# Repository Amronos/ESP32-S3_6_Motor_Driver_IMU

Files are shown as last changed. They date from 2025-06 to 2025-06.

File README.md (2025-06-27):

# ESP32-S3 6 Motor Driver with IMU

**_This board is currently in development._**

This board features an **ESP32-S3** microcontroller, a **6-channel** DC **motor driver**, and an integrated **BNO086 IMU** for precise motion and orientation data.<br>
It supports **encoder feedback**, enabling accurate position control. Motors can be driven at voltages up to **36V**.

This board is perfect for robots requiring more than two motors.<br>
Simply wire your motors, connect the board to a PC, another microcontroller, or even your phone/tablet and use the ESP32-S3's versatile communication options like I2C, SPI, UART, Wi-Fi, and Bluetooth to control your robot.

A full **Arduino library** for the board is available that allows you to control the motors, IMU, and read data from the encoders.<br>
Sample **ROS 2** packages are also available, that show the recommended usage of the board with ROS 2.

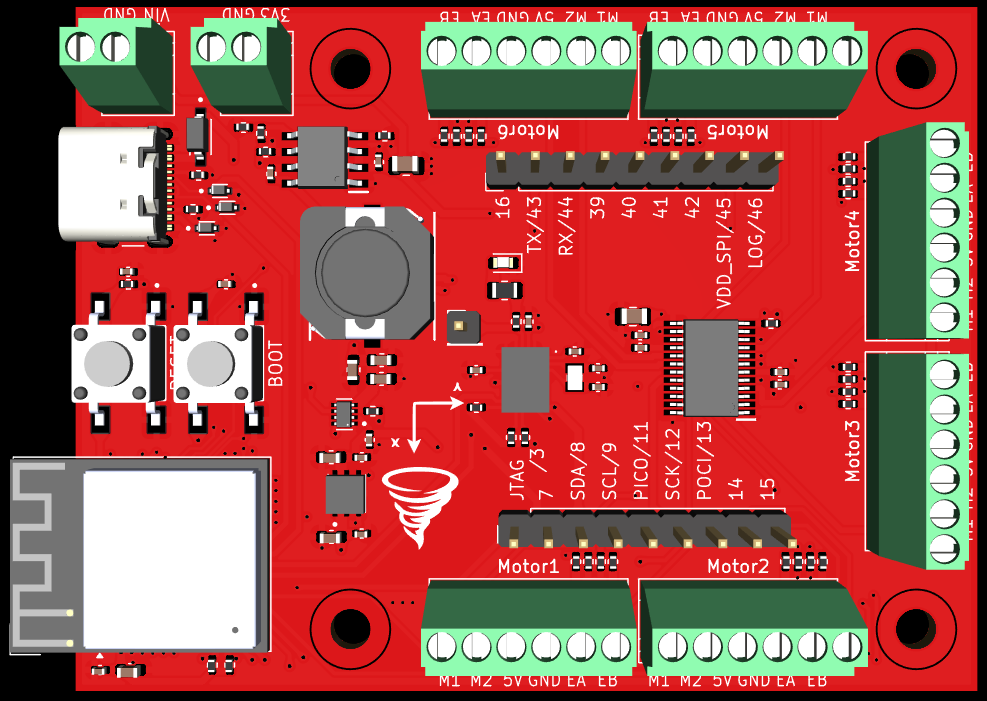
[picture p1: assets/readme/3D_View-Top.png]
3D Model - Top


## 📂 About this Repository

This repository contains all code, design files, and information related to the ESP32-S3 6 Motor Driver with IMU.

### Directory Information

- [assets/](assets/): Assets used throughout this repository.
- [hardware_design/](hardware_design/): Complete KiCad project design files, schematic, 3D model, and BOM.

### Related Repositories

- [ESP32-S3_6_Motor_Driver_IMU_Library](https://github.com/amronos/ESP32-S3_6_Motor_Driver_IMU_Library/): Arduino library for the board.

## 📷 Images

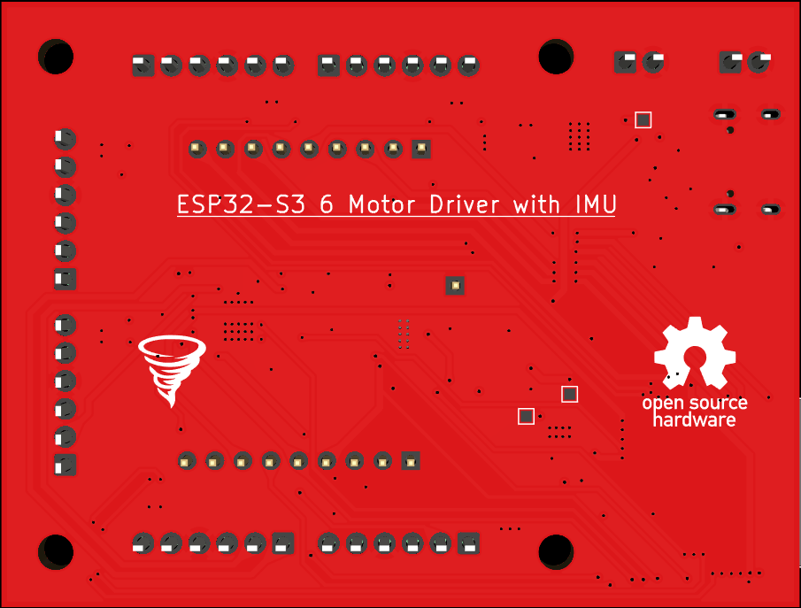
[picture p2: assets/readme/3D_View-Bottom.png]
3D Model - Bottom

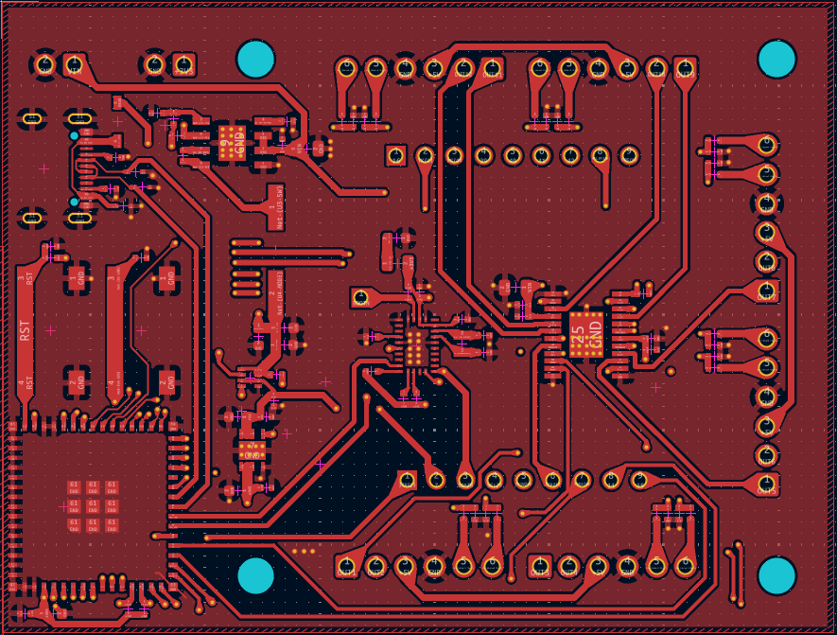
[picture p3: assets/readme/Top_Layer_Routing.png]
Top Layer Routing


## Costs

| Item | Price (USD) |
| --- | --- |
| Full PCB Manufacturing | $ 113.79 |
| Shipping | $ 25 |
| **Subtotal** | $ 138.79 |

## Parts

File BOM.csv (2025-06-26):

Designator | Footprint | Value | Manufacturer | Mfr. Part No. | Quantity
C1, C16 | 0805 | 10 µF | Murata Electronics | GRM21BR61H106KE43L | 2
C10, C11, C13, C15, C17, C18, C2, C21, C23, C24, C25, C3, C8, C9 | 0402 | 100 nF | Samsung Electro-Mechanics | CL05B104KB54PNC | 14
C12, C14, C7 | 0603 | 10 µF | Murata Electronics | GRT188R61E106ME13D | 3
C19 | 0402 | 4.7 µF | Murata Electronics | GRT155R61A475ME13D | 1
C20, C22 | 0402 | 22 pF | Murata Electronics | GCM1555C1H220FA16D | 2
C4, C5, C6 | 0603 | 22 µF | Murata Electronics | GRT188R61A226ME13D | 3
D1 | SOD3715X145N | 1N5819HW-7-F | Diodes Incorporated | 1N5819HW-7-F | 1
D2, D3, D4 | TVS_LESD5D5.0CT1G | LESD5D5.0CT1G | LRC | LESD5D5.0CT1G | 3
D5 | 0603 | LED | ROHM Semiconductor | SML-D12V8WT86C | 1
J1 | USB_C_Receptacle_GCT_USB4105-xx-A_16P_TopMnt_Horizontal | USB_C_Receptacle_USB2.0_16P | GCT | USB4105-GF-A | 1
J2, J3 | PinHeader_1x09_P2.54mm_Vertical | Conn_01x09 | Generic | Generic | 2
J4 | PinHeader_1x01_P2.54mm_Vertical | Conn_01x01 | Generic | Generic | 1
J5, J6 | TerminalBlock_Xinya_XY308-2.54-2P_1x02_P2.54mm_Horizontal | Screw_Terminal_01x02 | XINYA | XY308-2.54-2P | 2
L1 | INDPM102100X400N | 15 µH | Coilcraft | MSS1038-153MLC | 1
MOTOR1, MOTOR2, MOTOR3, MOTOR4, MOTOR5, MOTOR6 | TerminalBlock_Xinya_XY308-2.54-6P_1x06_P2.54mm_Horizontal | Screw_Terminal_01x06 | XINYA | XY308-2.54-6P | 6
R1, R2 | 0402 | 5.1 kΩ | Panasonic Electronic Components | ERA-2AED512X | 2
R10, R15, R16, R20, R22, R24, R26, R28, R3, R30, R32, R34, R36, R38, R39, R4, R5, R9 | 0402 | 10 kΩ | Panasonic Electronic Components | ERA-2AEB103X | 18
R11, R12, R17, R18 | 0402 | 4.7 kΩ | Panasonic Electronic Components | ERA-2AEB472X | 4
R13, R14, R19, R21, R23, R25, R27, R29, R31, R33, R35, R37 | 0402 | 20 kΩ | Panasonic Electronic Components | ERA-2AEB203X | 12
R40 | 0603 | 51 Ω | Panasonic Electronic Components | ERA-3AEB510V | 1
R6 | 0402 | 64.9 kΩ | Panasonic Electronic Components | ERA-2AEB6492X | 1
R7 | 0402 | 100 kΩ | Panasonic Electronic Components | ERA-2AEB104X | 1
R8 | 0402 | 24.9 kΩ | Panasonic Electronic Components | ERA-2AEB2492X | 1
SW1, SW2 | SW_3-1437565-0 | 3-1437565-0 | TE Connectivity | 3-1437565-0 | 2
U1 | ESP32-S2-MINI-1 | ESP32-S3-MINI-1 | Espressif Systems | ESP32-S3-MINI-1-N8 | 1
U2 | SON95P300X300X100-7N | LD39200PU33R | STMicroelectronics | LD39200PU33R | 1
U3 | SOIC127P600X170-9N | LMR38020FDDAR | Texas Instruments | LMR38020FDDAR | 1
U4 | SOTFL50P160X60-8N | TPS2116DRLR | Texas Instruments | TPS2116DRLR | 1
U5 | SOP65P640X120-25N | DRV8912QPWPRQ1 | Texas Instruments | DRV8912QPWPRQ1 | 1
U6 | BNO086 | BNO086 | Ceva | BNO086 | 1
Y1 | CM8V32768TA020125 | 32.768 kHz | Micro Crystal | CM8V-T1A-32.768kHz-12.5pF-20PPM-TB-QA | 1

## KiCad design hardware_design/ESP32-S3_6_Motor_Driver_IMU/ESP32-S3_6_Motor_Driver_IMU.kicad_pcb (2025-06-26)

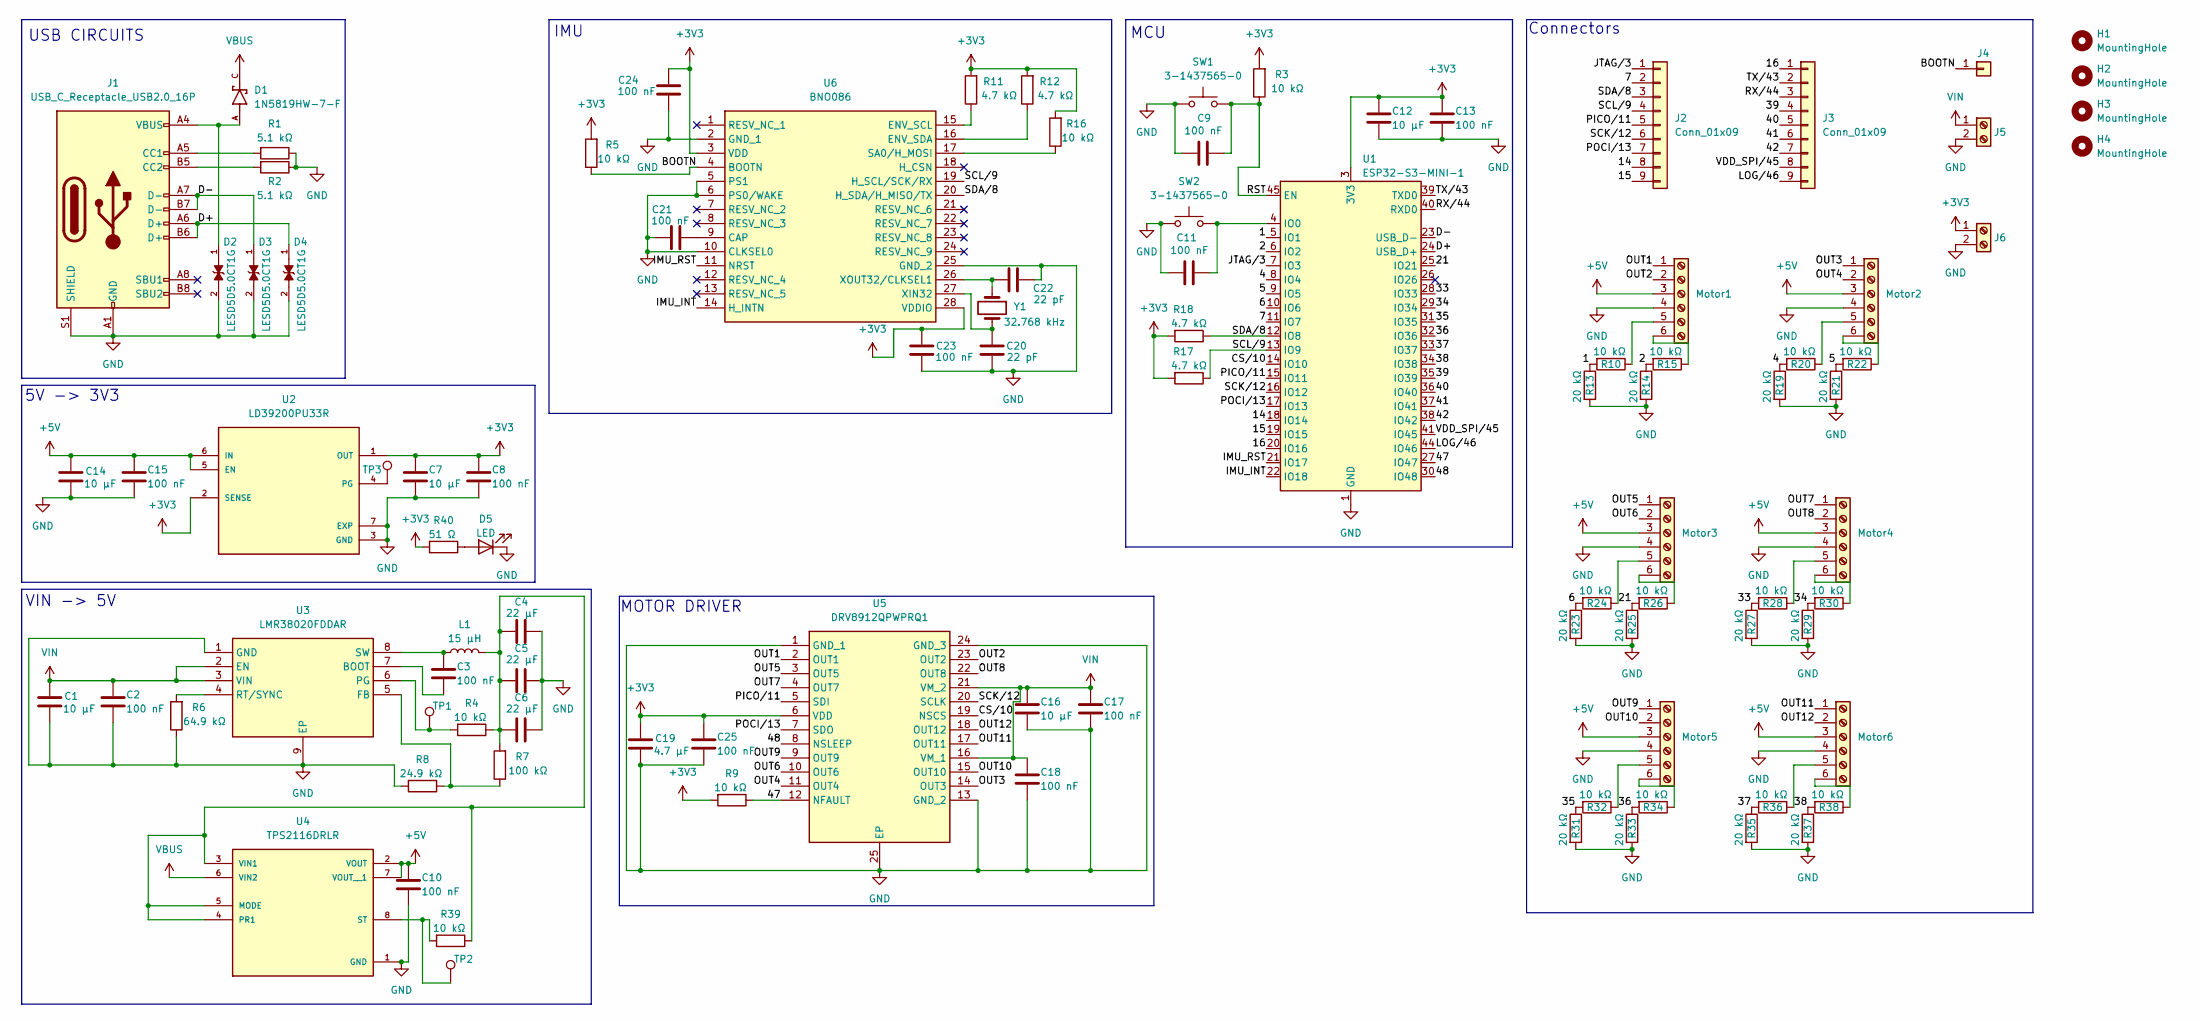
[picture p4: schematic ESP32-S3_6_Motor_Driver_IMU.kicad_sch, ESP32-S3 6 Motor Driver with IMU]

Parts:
C1, C16: 10 µF; C_0805_2012Metric
C2, C3, C8, C9, C10, C11, C13, C15, C17, C18, C21, C23, C24, C25: 100 nF; C_0402_1005Metric
C4, C5, C6: 22 µF; C_0603_1608Metric
C7, C12, C14: 10 µF; C_0603_1608Metric
C19: 4.7 µF; C_0402_1005Metric
C20, C22: 22 pF; C_0402_1005Metric
D1: 1N5819HW-7-F; SOD3715X145N
D2, D3, D4: LESD5D5.0CT1G; TVS_LESD5D5.0CT1G
D5: LED; LED_0603_1608Metric
H1, H2, H3, H4: MountingHole; MountingHole_3.2mm_M3
J1: USB_C_Receptacle_USB2.0_16P; USB_C_Receptacle_GCT_USB4105-xx-A_16P_TopMnt_Horizontal
J2, J3: Conn_01x09; PinHeader_1x09_P2.54mm_Vertical
J4: Conn_01x01; PinHeader_1x01_P2.54mm_Vertical
J5, J6: Screw_Terminal_01x02; TerminalBlock_Xinya_XY308-2.54-2P_1x02_P2.54mm_Horizontal
L1: 15 µH; INDPM102100X400N
Motor1, Motor2, Motor3, Motor4, Motor5, Motor6: Screw_Terminal_01x06; TerminalBlock_Xinya_XY308-2.54-6P_1x06_P2.54mm_Horizontal
R1, R2: 5.1 kΩ; R_0402_1005Metric
R3, R4, R5, R9, R10, R15, R16, R20, R22, R24, R26, R28, R30, R32, R34, R36, R38, R39: 10 kΩ; R_0402_1005Metric
R6: 64.9 kΩ; R_0402_1005Metric
R7: 100 kΩ; R_0402_1005Metric
R8: 24.9 kΩ; R_0402_1005Metric
R11, R12, R17, R18: 4.7 kΩ; R_0402_1005Metric
R13, R14, R19, R21, R23, R25, R27, R29, R31, R33, R35, R37: 20 kΩ; R_0402_1005Metric
R40: 51 Ω; R_0805_2012Metric
SW1, SW2: 3-1437565-0; SW_3-1437565-0
TP1, TP2, TP3: TestPoint; TestPoint_Pad_1.0x1.0mm
U1: ESP32-S3-MINI-1; ESP32-S2-MINI-1
U2: LD39200PU33R; SON95P300X300X100-7N
U3: LMR38020FDDAR; SOIC127P600X170-9N
U4: TPS2116DRLR; SOTFL50P160X60-8N
U5: DRV8912QPWPRQ1; SOP65P640X120-25N
U6: BNO086
Y1: 32.768 kHz; CM8V32768TA020125

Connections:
+3V3: C7.1, C8.1, C12.1, C13.1, C19.1, C23.1, C24.2, C25.1, J6.1, R3.2, R5.2, R9.2, R11.2, R12.2, R16.2, R17.2, R18.2, R40.2, U1.3 (3V3), U2.1 (OUT), U2.2 (SENSE), U5.6 (VDD), U6.3 (VDD), U6.28 (VDDIO)
+5V: C10.1, C14.1, C15.1, Motor1.3, Motor2.3, Motor3.3, Motor4.3, Motor5.3, Motor6.3, U2.5 (EN), U2.6 (IN), U4.2 (VOUT), U4.7 (VOUT__1)
/1: R10.2, R13.1, U1.5 (IO1)
/2: R14.1, R15.2, U1.6 (IO2)
/4: R19.1, R20.2, U1.8 (IO4)
/5: R21.1, R22.2, U1.9 (IO5)
/6: R23.1, R24.2, U1.10 (IO6)
/7: J2.2, U1.11 (IO7)
/14: J2.8, U1.18 (IO14)
/15: J2.9, U1.19 (IO15)
/16: J3.1, U1.20 (IO16)
/21: R25.1, R26.2, U1.25 (IO21)
/33: R27.1, R28.2, U1.28 (IO33)
/34: R29.1, R30.2, U1.29 (IO34)
/35: R31.1, R32.2, U1.31 (IO35)
/36: R33.1, R34.2, U1.32 (IO36)
/37: R35.1, R36.2, U1.33 (IO37)
/38: R37.1, R38.2, U1.34 (IO38)
/39: J3.4, U1.35 (IO39)
/40: J3.5, U1.36 (IO40)
/41: J3.6, U1.37 (IO41)
/42: J3.7, U1.38 (IO42)
/47: R9.1, U1.27 (IO47), U5.12 (NFAULT)
/48: U1.30 (IO48), U5.8 (NSLEEP)
/BOOTN: J4.1, R5.1, U6.4 (BOOTN)
/CS/10: U1.14 (IO10), U5.19 (NSCS)
/D+: D4.1, J1.A6 (D+), J1.B6 (D+), U1.24 (USB_D+)
/D-: D3.1, J1.A7 (D-), J1.B7 (D-), U1.23 (USB_D-)
/IMU_INT: U1.22 (IO18), U6.14 (H_INTN)
/IMU_RST: U1.21 (IO17), U6.11 (NRST)
/JTAG/3: J2.1, U1.7 (IO3)
/LOG/46: J3.9, U1.44 (IO46)
/OUT1: Motor1.1, U5.2 (OUT1)
/OUT2: Motor1.2, U5.23 (OUT2)
/OUT3: Motor2.1, U5.14 (OUT3)
/OUT4: Motor2.2, U5.11 (OUT4)
/OUT5: Motor3.1, U5.3 (OUT5)
/OUT6: Motor3.2, U5.10 (OUT6)
/OUT7: Motor4.1, U5.4 (OUT7)
/OUT8: Motor4.2, U5.22 (OUT8)
/OUT9: Motor5.1, U5.9 (OUT9)
/OUT10: Motor5.2, U5.15 (OUT10)
/OUT11: Motor6.1, U5.17 (OUT11)
/OUT12: Motor6.2, U5.18 (OUT12)
/PICO/11: J2.5, U1.15 (IO11), U5.5 (SDI)
/POCI/13: J2.7, U1.17 (IO13), U5.7 (SDO)
/RST: C9.2, R3.1, SW1.3 (B), SW1.4 (B), U1.45 (EN)
/RX/44: J3.3, U1.40 (RXD0)
/SCK/12: J2.6, U1.16 (IO12), U5.20 (SCLK)
/SCL/9: J2.4, R17.1, U1.13 (IO9), U6.19 (H_SCL/SCK/RX)
/SDA/8: J2.3, R18.1, U1.12 (IO8), U6.20 (H_SDA/H_MISO/TX)
/TX/43: J3.2, U1.39 (TXD0)
/VDD_SPI/45: J3.8, U1.41 (IO45)
GND: C1.2, C2.2, C4.2, C5.2, C6.2, C7.2, C8.2, C9.1, C10.2, C11.1, C12.2, C13.2, C14.2, C15.2, C16.2, C17.2, C18.2, C19.2, C20.2, C21.1, C22.2, C23.2, C24.1, C25.2, D2.2, D3.2, D4.2, D5.1 (K), J1.A1 (GND), J1.A12 (GND), J1.B1 (GND), J1.B12 (GND), J1.S1 (SHIELD), J5.2, J6.2, Motor1.4, Motor2.4, Motor3.4, Motor4.4, Motor5.4, Motor6.4, R1.1, R2.1, R6.1, R8.2, R13.2, R14.2, R19.2, R21.2, R23.2, R25.2, R27.2, R29.2, R31.2, R33.2, R35.2, R37.2, SW1.1 (A), SW1.2 (A), SW2.1 (A), SW2.2 (A), U1.1 (GND), U1.2 (GND), U1.42 (GND), U1.43 (GND), U1.46 (GND), U1.47 (GND), U1.48 (GND), U1.49 (GND), U1.50 (GND), U1.51 (GND), U1.52 (GND), U1.53 (GND), U1.54 (GND), U1.55 (GND), U1.56 (GND), U1.57 (GND), U1.58 (GND), U1.59 (GND), U1.60 (GND), U1.61 (GND), U1.62 (GND), U1.63 (GND), U1.64 (GND), U1.65 (GND), U2.3 (GND), U2.7 (EXP), U3.1 (GND), U3.9 (EP), U4.1 (GND), U5.1 (GND_1), U5.13 (GND_2), U5.24 (GND_3), U5.25 (EP), U6.2 (GND_1), U6.5 (PS1), U6.6 (PS0/WAKE), U6.10 (CLKSEL0), U6.25 (GND_2)
unnamed: D1.A, D2.1, J1.A4 (VBUS), J1.A9 (VBUS), J1.B4 (VBUS), J1.B9 (VBUS)
unnamed: D5.2 (A), R40.1
unnamed: J1.A5 (CC1), R1.2
unnamed: J1.B5 (CC2), R2.2
unnamed: Motor1.5, R10.1
unnamed: Motor1.6, R15.1
unnamed: Motor2.5, R20.1
unnamed: Motor2.6, R22.1
unnamed: Motor3.5, R24.1
unnamed: Motor3.6, R26.1
unnamed: Motor4.5, R28.1
unnamed: Motor4.6, R30.1
unnamed: Motor5.5, R32.1
unnamed: Motor5.6, R34.1
unnamed: Motor6.5, R36.1
unnamed: Motor6.6, R38.1
unnamed: C11.2, SW2.3 (B), SW2.4 (B), U1.4 (IO0)
unnamed: TP3.1, U2.4 (PG)
unnamed: C3.2, U3.7 (BOOT)
unnamed: R7.1, R8.1, U3.5 (FB)
unnamed: R4.2, TP1.1, U3.6 (PG)
unnamed: R6.2, U3.4 (RT/SYNC)
unnamed: C3.1, L1.1, U3.8 (SW)
unnamed: C4.1, C5.1, C6.1, L1.2, R4.1, R7.2, R39.1, U4.3 (VIN1), U4.4 (PR1), U4.5 (MODE)
unnamed: R39.2, TP2.1, U4.8 (ST)
unnamed: C21.2, U6.9 (CAP)
unnamed: R11.1, U6.15 (ENV_SCL)
unnamed: R12.1, U6.16 (ENV_SDA)
unnamed: R16.1, U6.17 (SA0/H_MOSI)
unnamed: C20.1, U6.27 (XIN32), Y1.2
unnamed: C22.1, U6.26 (XOUT32/CLKSEL1), Y1.1
VBUS: D1.C, U4.6 (VIN2)
VIN: C1.1, C2.1, C16.1, C17.1, C18.1, J5.1, U3.2 (EN), U3.3 (VIN), U5.16 (VM_1), U5.21 (VM_2)

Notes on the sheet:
MCU
USB CIRCUITS
Connectors
IMU
VIN -> 5V
5V -> 3V3
MOTOR DRIVER

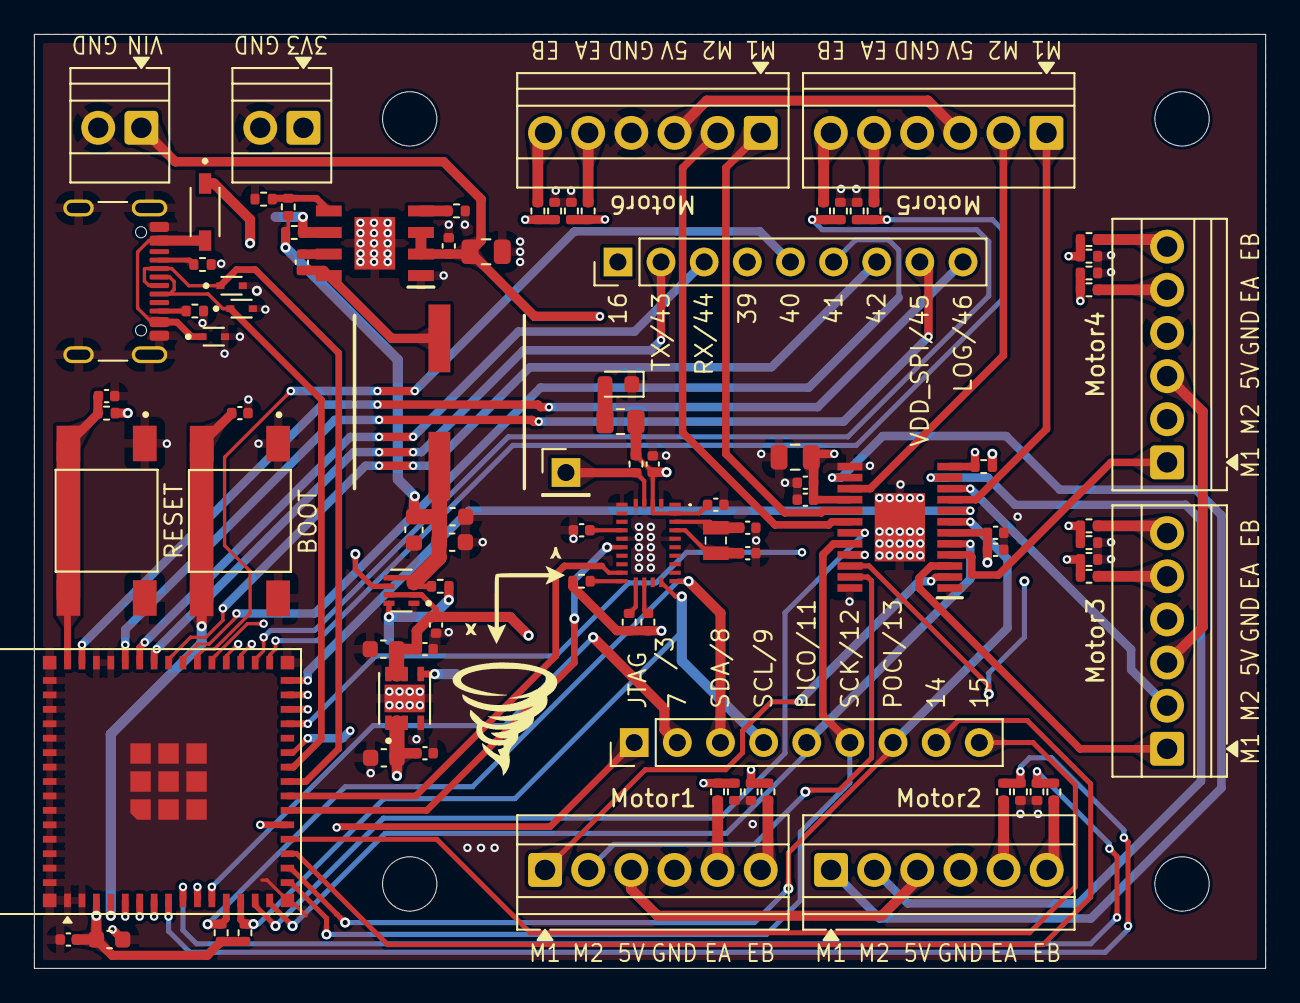
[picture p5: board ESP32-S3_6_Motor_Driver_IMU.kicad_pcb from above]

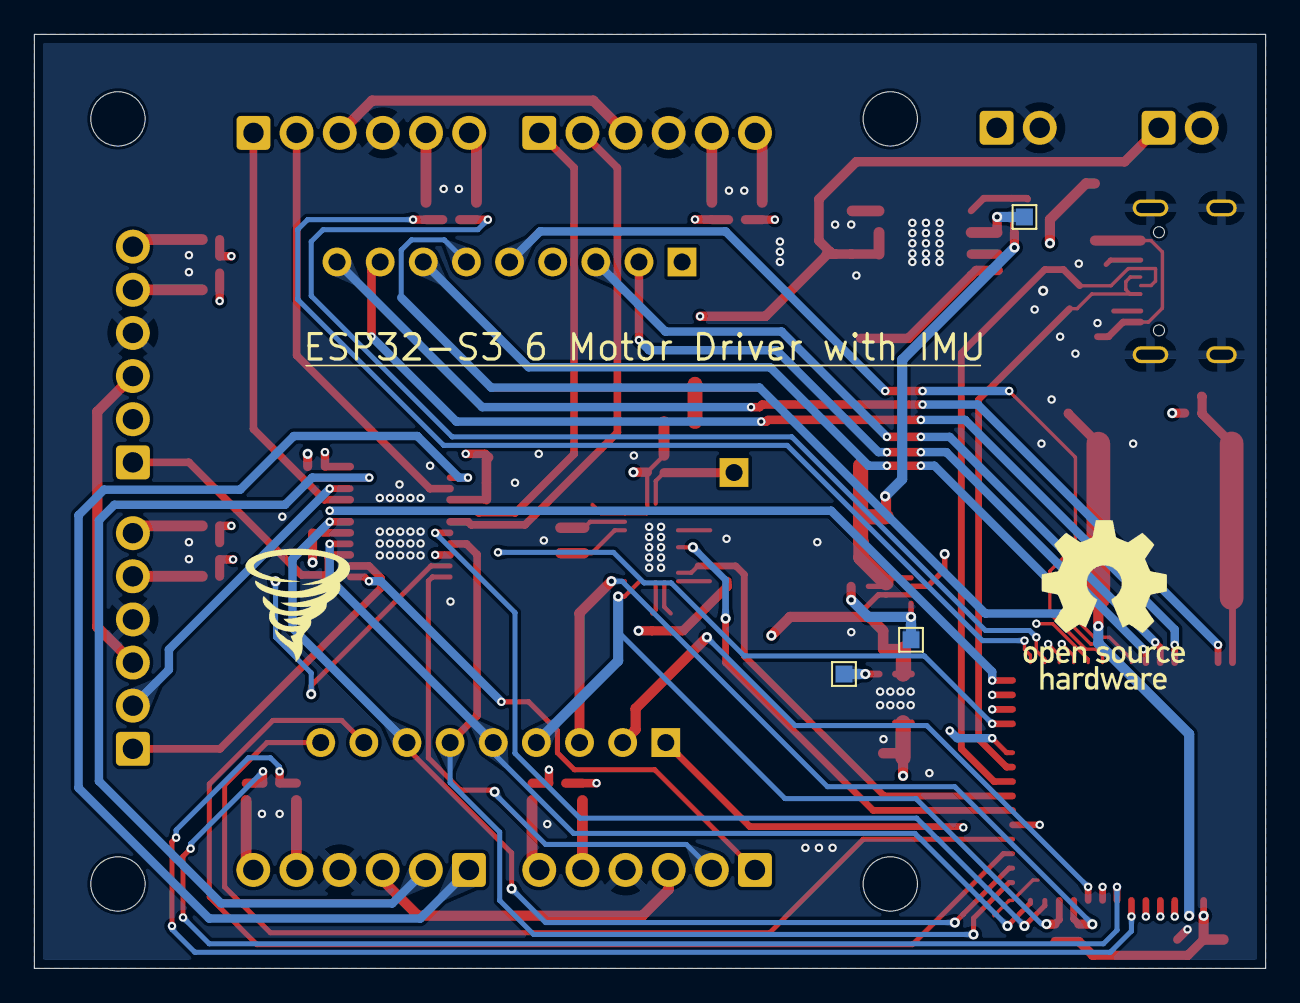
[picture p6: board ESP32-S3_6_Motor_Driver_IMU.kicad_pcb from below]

Board: 4 copper layers, 72.5 x 55.0 mm, 99 parts (3 on the bottom side), 87 nets.

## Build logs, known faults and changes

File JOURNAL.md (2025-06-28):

---
title: "ESP32-S3 6 Motor Driver with IMU"
author: "Aarav Gupta"
description: "A board featuring an ESP32-S3, a 6-channel DC motor driver, an integrated IMU, and support for encoder feedback."
created_at: "2025-06-17"
total_time_spent: 31 hours
---

## 26th June 2025: Minor Improvements

Today I added X-Y axes for the IMU to the PCB's silkscreen alongside adding some more thermal vias.<br>
I also fully completed the BOM.

**Total time spent: 1.5h**

## 24th June 2025: Started Working on Library

I started working on the Arduino library for the board today. It is/will be a wrapper around other libraries that are used to control the BNO086 and DRV8912-Q1.<br>
Today I created functions in the library for easily getting data from the IMU and printing it alongside an example Arduino sketch.<br>
I am using the [SparkFun BNO08x Cortex Based IMU Library](https://github.com/sparkfun/SparkFun_BNO08x_Arduino_Library) for the BNO086 and will creating my own library for the DRV8912-Q1.

**Total time spent: 4h**

## 23rd June 2025: Created BOM

Today I created the almost final BOM for the board containing all the components used on the board.

**Total time spent: 3h**

## 21st to 22nd June 2025: Completed PCB

I spent these 2 days completing the PCB layout and routing all the tracks. The routing got pretty hard with the last 10 to 15 tracks and I had to use both of the inner layers to successfully route the PCB.

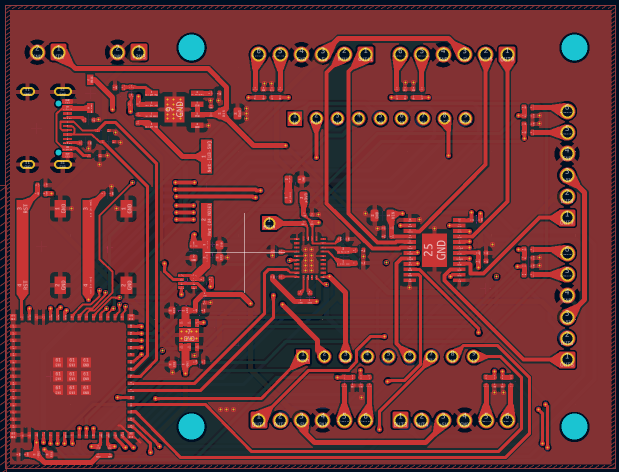
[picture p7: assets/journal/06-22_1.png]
Layer 1
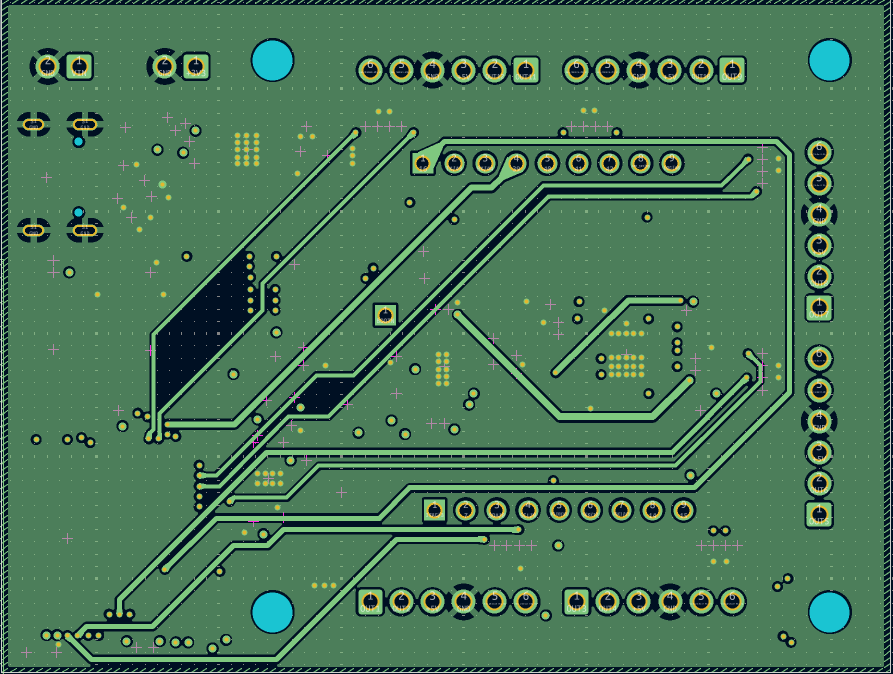
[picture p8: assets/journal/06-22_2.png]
Layer 2
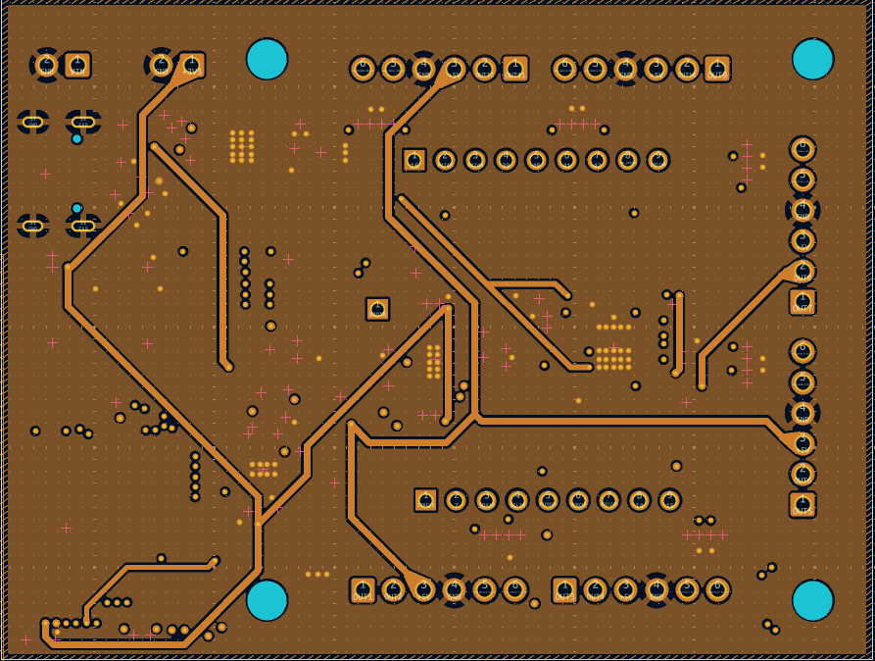
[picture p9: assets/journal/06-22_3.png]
Layer 3
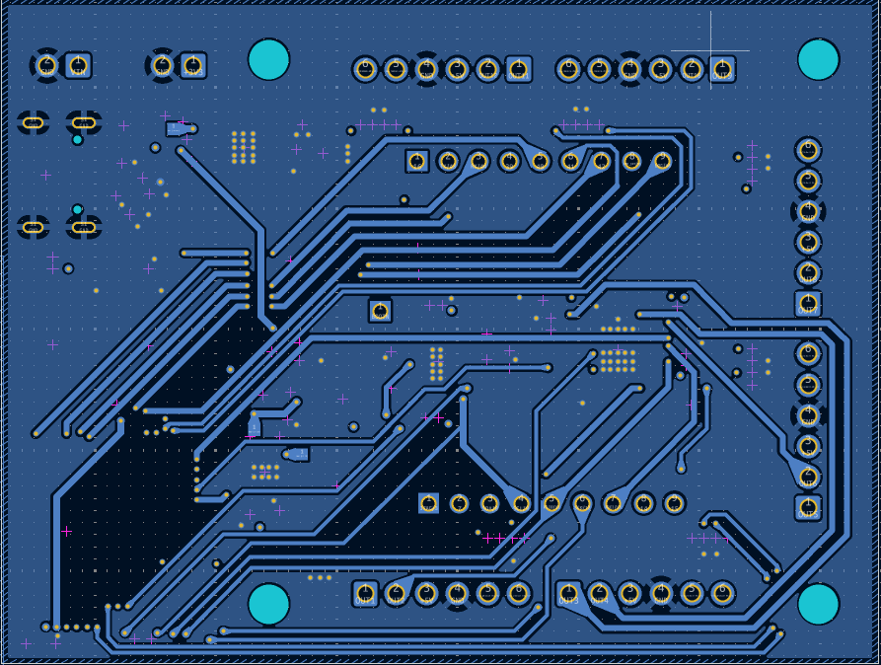
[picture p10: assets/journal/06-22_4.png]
Layer 4
|  |  |  |  |
| :---: | :---: | :---: | :---: |
| Layer 1 | Layer 2 | Layer 3 | Layer 4 |

**Total time spent: 8h**

## 20th June 2025: Made Fixes to the Schematic

I did a final review of the schematic today and did the needed fixes alongside adding test points and LEDs. I also routed some of the PCB today.

**Total time spent: 5h**

## 19th June 2025: Completed Placement of Connector Components

Today I first placed the ESP32-S3 on the bottom right of the PCB similar to the recommendation in the application information. Then I placed the various types of connectors symetrically on the board, alongside positioning the screw holes.

**Total time spent: 2h**

## 18th June 2025: Created a Diagram Showing ROS 2 Usage

Today I created a diagram showing how the board will be used with ROS 2, this will be useful to create the ROS 2 code to be used with this board.
I also made some fixes to the schematic.

| ROS 2 Usage Diagram |
| :-----------------------------------------------------: |
|                   ROS 2 Usage Diagram                   |

**Total time spent: 1.5h**

## 17th June 2025: Created Board Schematic

Today I created the full schematic for the board.
I settled on the following ICs: ESP32-S3, BNO086(IMU), DRV8912-Q1(Motor Driver), LMR38020FDDAR(5V Regulator), TPS2116DRLR(Power Mux for selecting between 5V from regulator and USB), LD39200PU33R(3.3V Regulator).

| Schematic |
| :--------------------------------------: |
|                Schematic                 |

**Total time spent: 6h**

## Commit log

2025-06-18 Complete schematic
    [ESP32-S3_6_Motor_Driver_IMU.kicad_pcb, ESP32-S3_6_Motor_Driver_IMU.kicad_sch]
2025-06-19 Add diagram showing ROS2 usage
    Also make fixes to schematic
    [ESP32-S3_6_Motor_Driver_IMU.kicad_sch]
2025-06-23 Complete PCB
    [ESP32-S3_6_Motor_Driver_IMU.kicad_pcb, ESP32-S3_6_Motor_Driver_IMU.kicad_sch, bom.csv]
2025-06-26 Make minor updates to the PCB
    [ESP32-S3_6_Motor_Driver_IMU.kicad_pcb]
2025-06-29 Move BOM.csv
    [BOM.csv]
